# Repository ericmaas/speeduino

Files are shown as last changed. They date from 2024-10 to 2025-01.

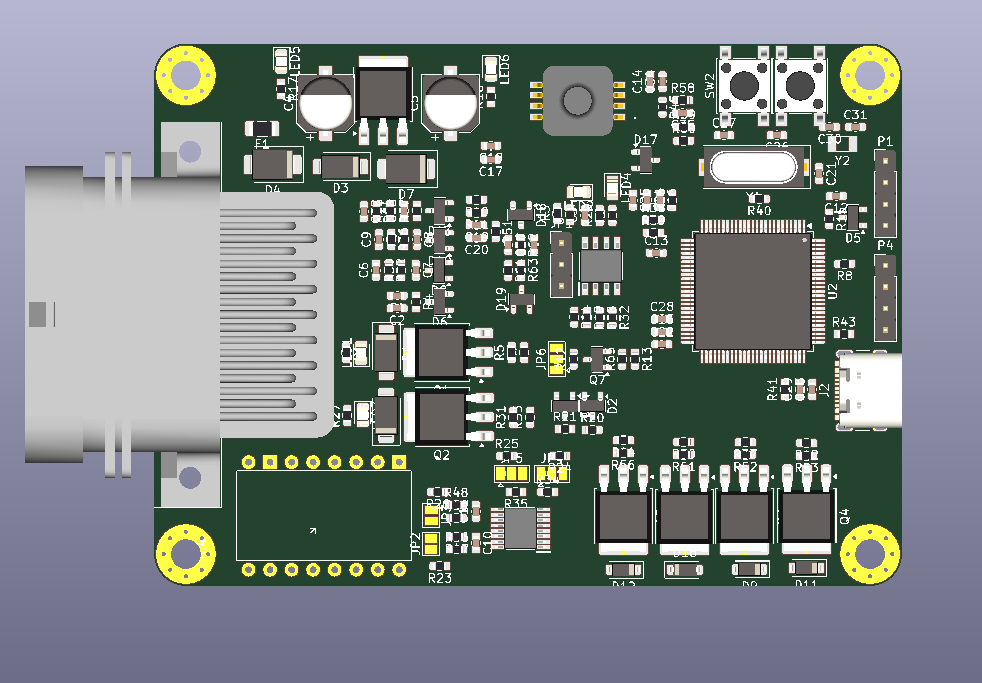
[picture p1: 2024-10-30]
NO2C-SMD/vDD1 - SMD/RENDER/Ideation/top-4layer-render.jpg

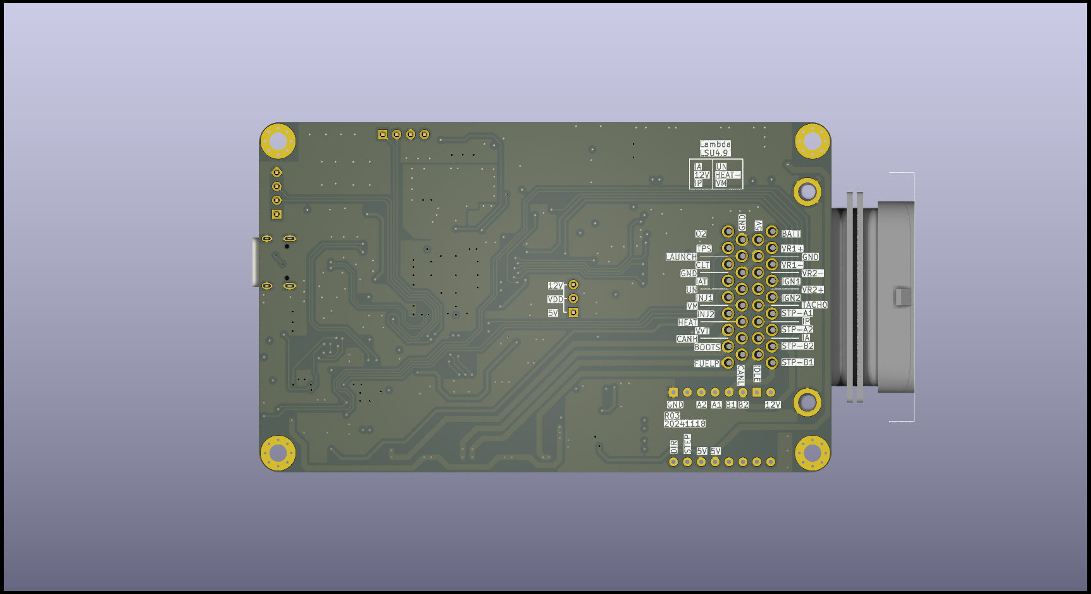
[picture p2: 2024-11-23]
NO2C-SMD/vDD3-SMDWBBT/RENDER/NO2C-2.png

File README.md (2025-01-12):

## NO2C vDD

All Credit to the Speeduino Team
https://github.com/speeduino/speeduino

And 

https://github.com/turboedge/SpeedyBoards/

Originally forked from:
https://github.com/turboedge/SpeedyBoards/tree/master

Wideband ideation from:
https://github.com/oelprinz-org

Please review my workprior to printing, and test your work. 

I am not an engineer, mechanic, or automotive specialist, please use at your own risk.

Please review vehicle laws and regulations prior to use. 

Connector used is a TE # 3-6437285-0

Future Feature Wish List:

- SD Card for data logging
- Dedicated prototyping pins (would be great for oil pressure)

The No Overhang Two Channel was designed to incorporate as many features as possible into a SMD board that moves to a new smaller format size. Microcontroller onboard. It is a 2+2 channel board that incorporates the features below.
- Two injector channels
- Two ignitor channels
- Outputs for VVT PWM idle, boost, fuel pump, and tachometer
- Two trigger inputs
- Launch input
- Analog inputs for CLT, IAT, TPS, and O2
- MAP sensor onboard
- Socket for stepper idle control module
- Additional pins for i2c and canbus
- LSU 4.9 Wideband integration
- Bluetooth 4.0 (HM-10)

Latest version: DD3

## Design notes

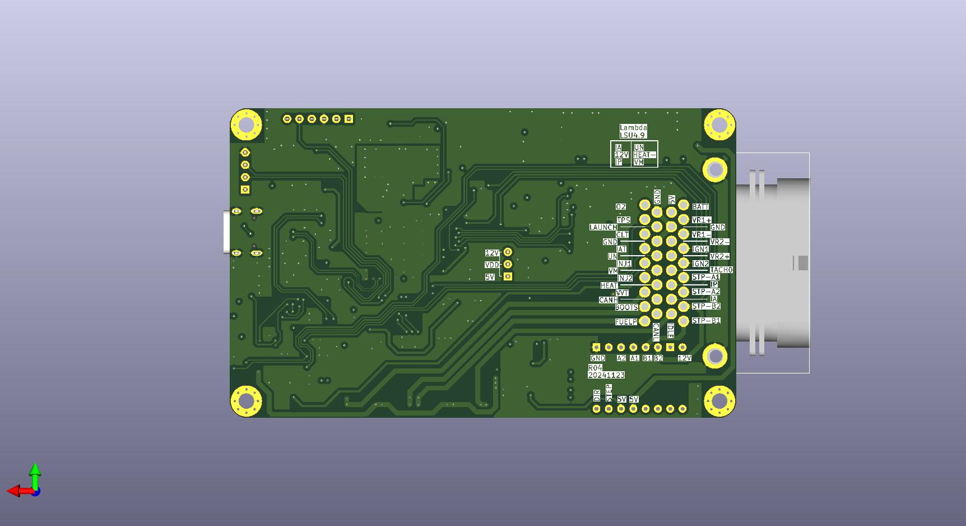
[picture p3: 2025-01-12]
NO2C-SMD/vDD3-SMDWBBT/RENDER/NO2C.jpg

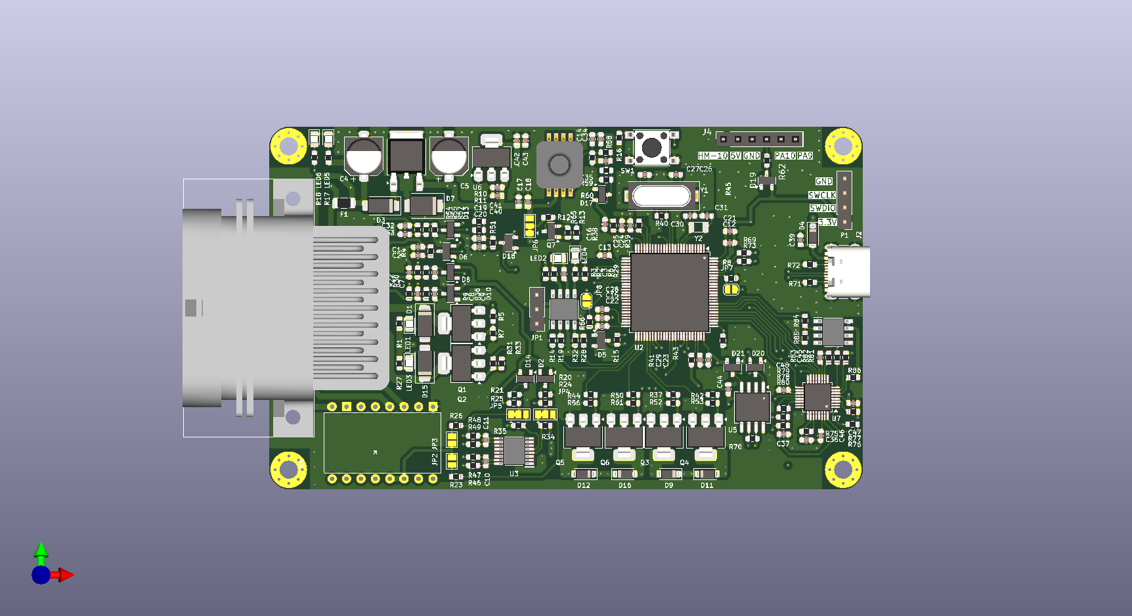
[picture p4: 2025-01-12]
NO2C-SMD/vDD3-SMDWBBT/RENDER/NO2C.png

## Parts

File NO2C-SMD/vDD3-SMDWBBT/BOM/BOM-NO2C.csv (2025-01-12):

Comment | Designator | Footprint | LCSC | Quantity
22pF | C26,C27 | C_0603_1608Metric | C105620 | 2
47pF | C14 | C_0603_1608Metric | C105622 | 1
12pF | C30,C31 | C_0603_1608Metric | C107034 | 2
220nF | C2,C20,C33,C35,C7,C9 | C_0603_1608Metric | C107083 | 6
10uF | C39,C41,C42 | C_0603_1608Metric | C109457 | 3
8Mhz | Y1 | Crystal_SMD_HC49-SD | C12674 | 1
2K7 | R17 | R_0603_1608Metric | C13167 | 1
60V 1A | D3 | D_SMA | C134421 | 1
100nF | C1,C13,C15,C16,C17,C18,C19,C21,C22,C23,C25,C28,C29,C3,C32,C34,C36,C40,C43,C44,C45,C46,C47,C48,C6,C8 | C_0603_1608Metric | C14663 | 26
MAX9926UAEE+ | U3 | SOP64P602X175-16N | C1523548 | 1
1A 60V | F1 | Fuse_1206_3216Metric | C163133 | 1
1nF | C10,C11,C12,C24 | C_0603_1608Metric | C1636 | 4
USB_C_Receptacle_USB2.0_16P | J2 | USB_C_Receptacle_GCT_USB4105-xx-A_16P_TopMnt_Horizontal | C165948 | 1
CJ125_32 | U7 | LQFP-32_5x5mm_P0.5mm | C18198890 | 1
0R | R38,R39 | R_0603_1608Metric | C21189 | 2
1K | R12,R14,R15,R23,R26,R28,R34,R35,R69,R73 | R_0603_1608Metric | C21190 | 10
100R | R13,R31,R37,R42,R44,R5,R50 | R_0603_1608Metric | C22775 | 7
120R | R70 | R_0603_1608Metric | C22787 | 1
2K49 | R22,R9 | R_0603_1608Metric | C22908 | 2
1M | R40 | R_0603_1608Metric | C22935 | 1
2K | R1,R2,R27,R6 | R_0603_1608Metric | C22975 | 4
61.9R | R76 | R_0603_1608Metric | C23092 | 1
4K7 | R55,R59 | R_0603_1608Metric | C23162 | 2
470R | R18,R24,R25,R30,R36,R4,R51,R54,R58,R62 | R_0603_1608Metric | C23179 | 10
47R | R29,R3 | R_0603_1608Metric | C23182 | 2
5.1K | R71,R72 | R_0603_1608Metric | C23186 | 2
51K | R11,R45 | R_0603_1608Metric | C23196 | 2
9K1 | R57,R60 | R_0603_1608Metric | C23260 | 2
100K | R19,R32,R75,R80,R85 | R_0603_1608Metric | C25803 | 5
10K | R16,R20,R21,R33,R41,R43,R46,R47,R48,R49,R52,R53,R56,R61,R65,R66,R7,R77,R8,R81,R82,R83 | R_0603_1608Metric | C25804 | 22
6.8K | R86 | R_0603_1608Metric | C26004 | 1
BSP78HUMA1 | Q1,Q2,Q3,Q4,Q5,Q6 | SOT-223-3_TabPin2 | C2653794 | 6
MPXH6400AC6T1 | IC2 | MPXH6400AC6T1 | C2828031 | 1
STM32F407VETx | U2 | LQFP-100_14x14mm_P0.5mm | C28730 | 1
1N4007-A7 | D11,D12,D16,D4,D9 | D_SOD-123 | C2902912 | 5
2.2nF | C37 | C_0603_1608Metric | C309517 | 1
32.768Khz | Y2 | Crystal_SMD_3215-2Pin_3.2x1.5mm | C32346 | 1
47u 50v | C4,C5 | CP_Elec_6.3x7.7 | C3349 | 2
AO3400A | Q7 | SOT-23 | C344010 | 1
470K | R78 | R_0603_1608Metric | C365173 | 1
HM-10 | J4 | PinSocket_1x06_P2.54mm_Vertical | C40877 | 1
33K | R10 | R_0603_1608Metric | C4216 | 1
TC4424AVOA | IC1 | SOIC127P600X175-8N | C44150 | 1
BAT54S | D10,D13,D14,D17,D18,D19,D2,D20,D21,D5,D6,D8 | SOT-23 | C47546 | 12
ING-VLT | JP1 | PinHeader_1x03_P2.54mm_Vertical | C49257 | 1
VNS3NV04DPTR-E | IC3 | SOIC127P600X175-8N | C503069 | 1
Conn_01x04 | P1 | PinHeader_1x04_P2.54mm_Vertical | C5116483 | 1
SW_Push | SW1 | SW_Push_1P1T_NO_6x6mm_H9.5mm | C5127964 | 1
AMS1117-3.3 | U6 | SOT-223-3_TabPin2 | C6186 | 1
TJA1050 | U5 | SO-8_5.3x6.2mm_P1.27mm | C6952 | 1
1N4004 | D1,D15 | D_SMA | C727080 | 2
L7805CDT(UMW) | U1 | TO-252-2 | C7394043 | 1
1SMB5919BT3G | D7 | D_SMB | C7422622 | 1
RED | LED1,LED2,LED3,LED4,LED5,LED6 | LED_0805_2012Metric | C84256 | 6
4.7K | R79,R84 | R_0603_1608Metric | C99782 | 2
3-6437285-0 | J1 | 364372850 |  | 1

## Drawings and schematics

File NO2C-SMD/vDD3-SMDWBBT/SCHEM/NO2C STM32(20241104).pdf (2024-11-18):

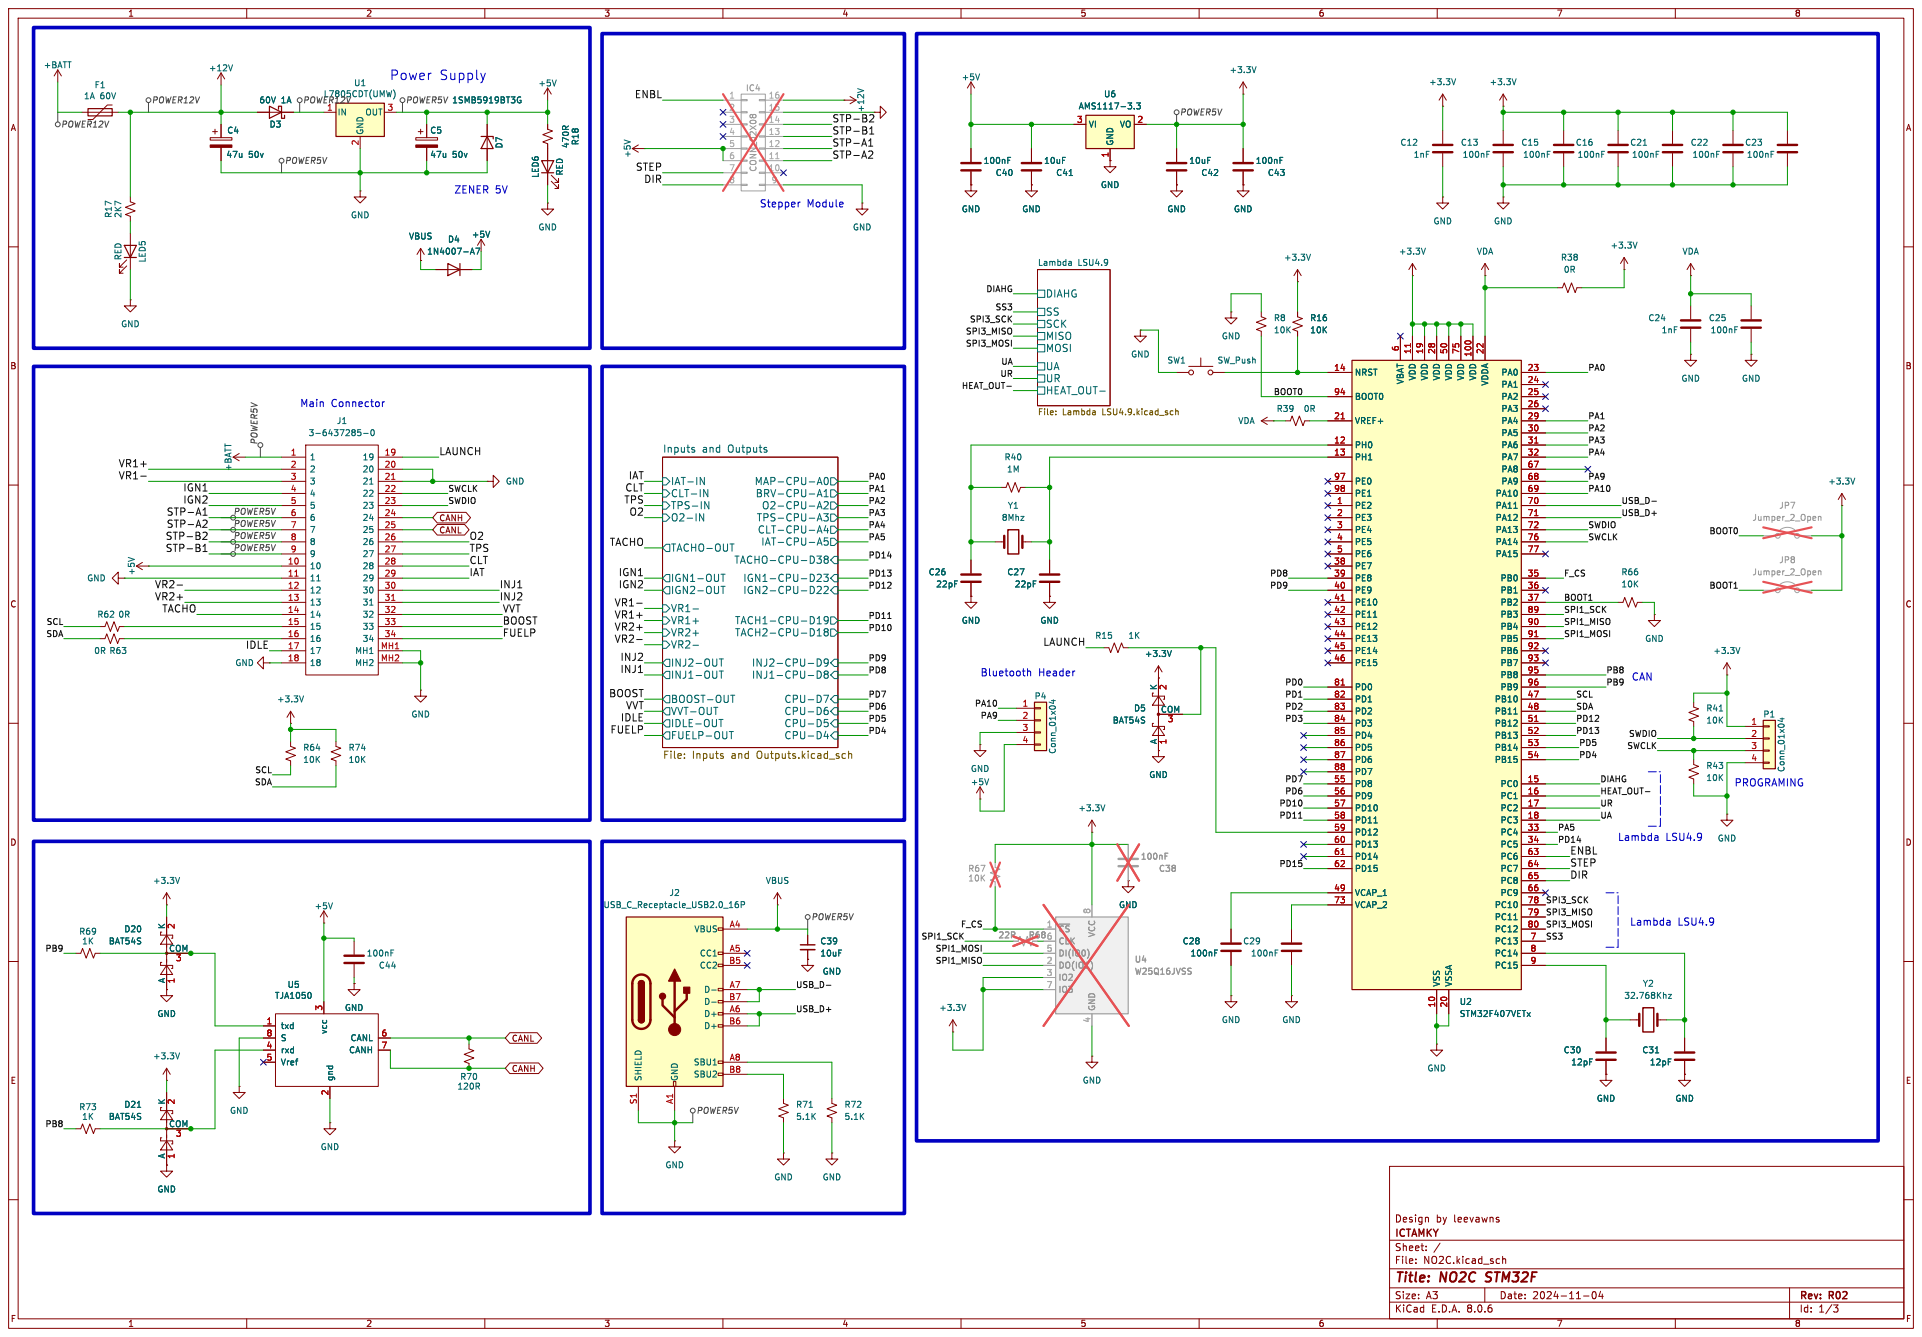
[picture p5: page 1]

Power Supply Main Connector

HEAT_OUT- Lambda LSU4.9 File: Lambda LSU4.9.kicad_sch GND GND

ICTAMKY Design by leevawns

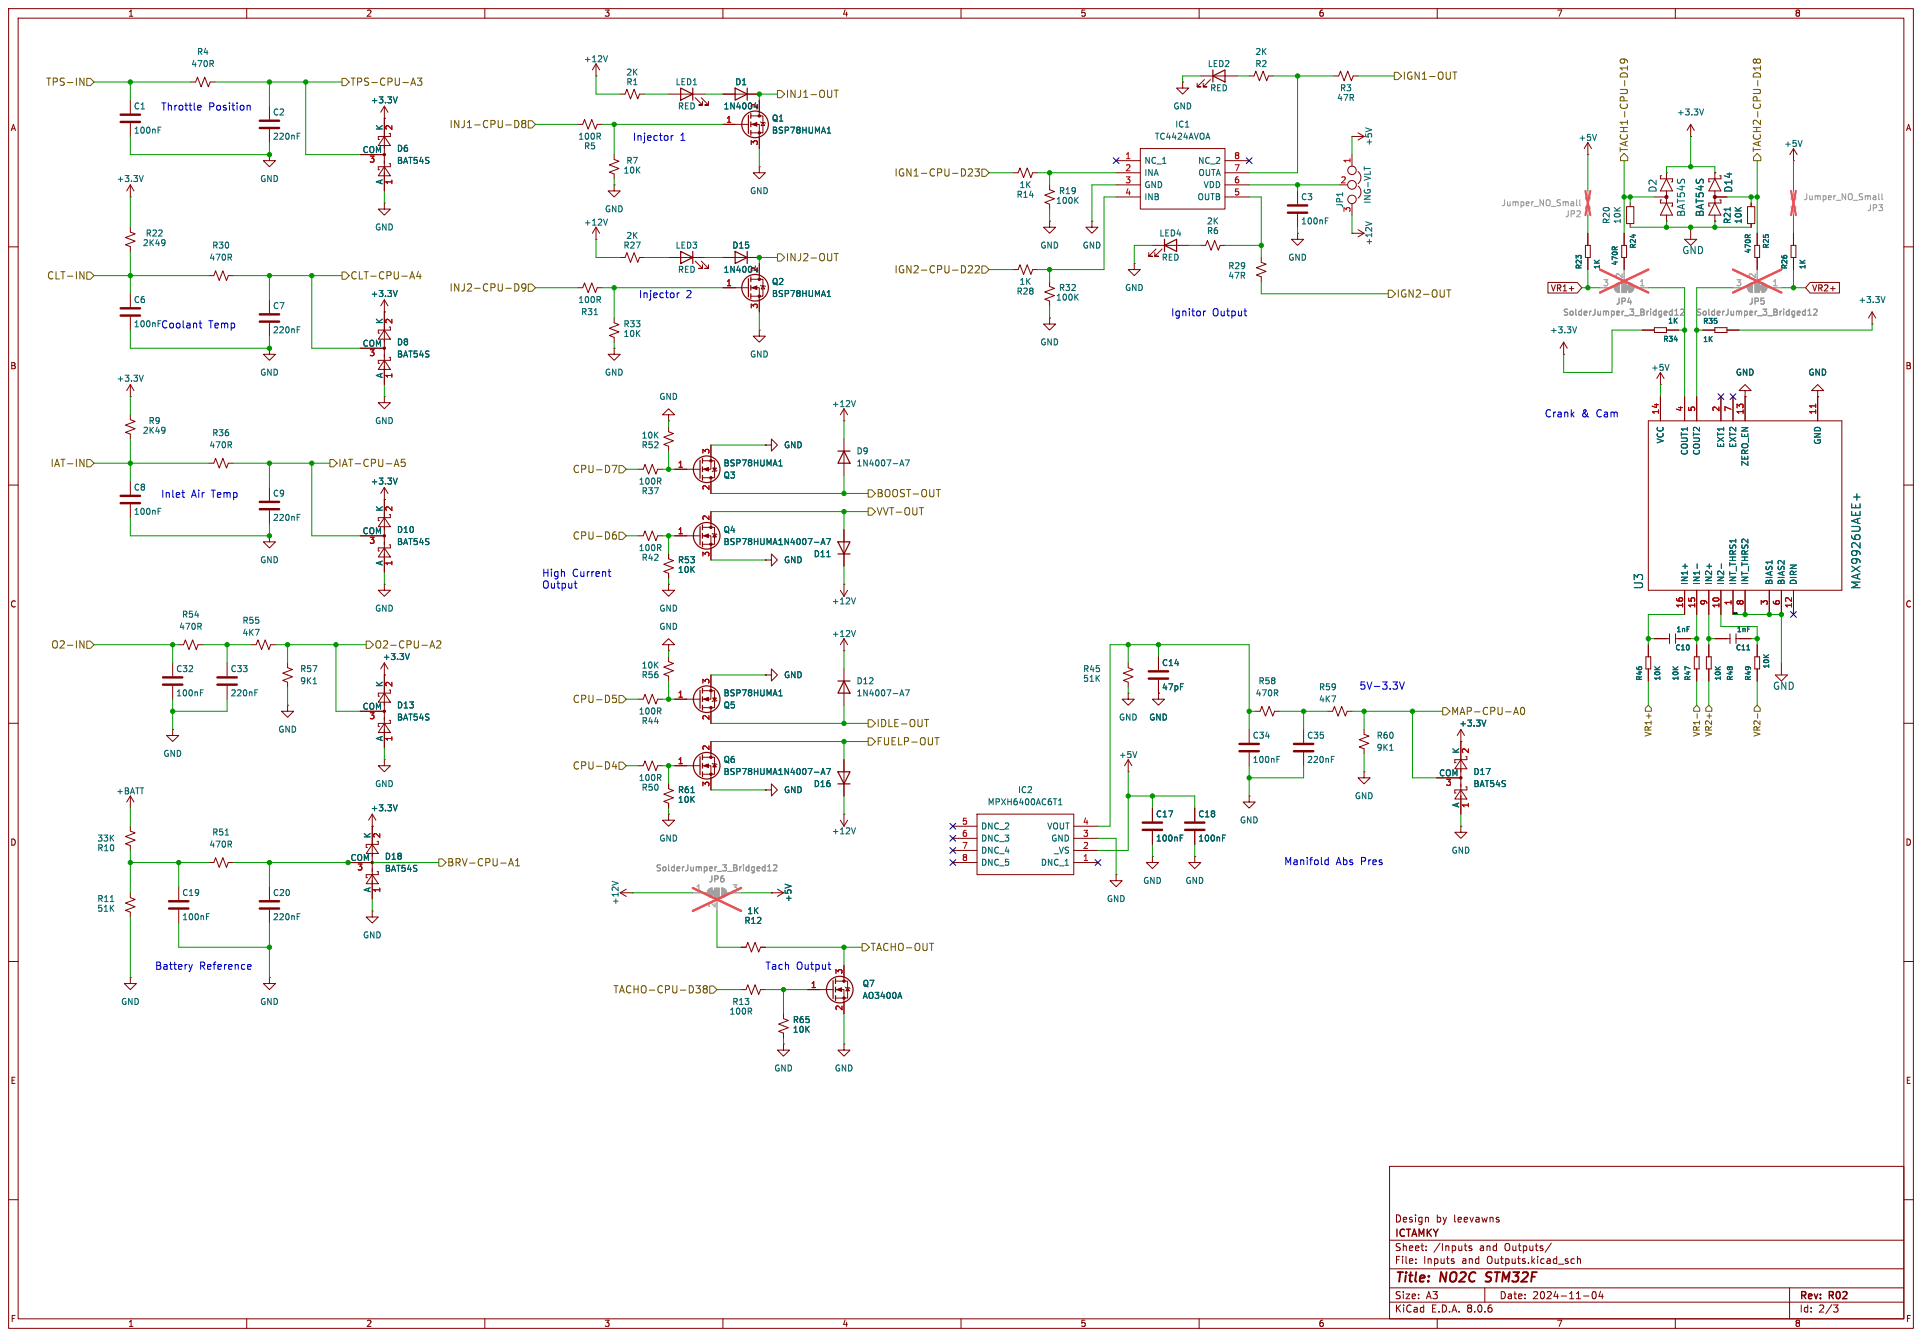
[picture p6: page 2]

ICTAMKY Design by leevawns

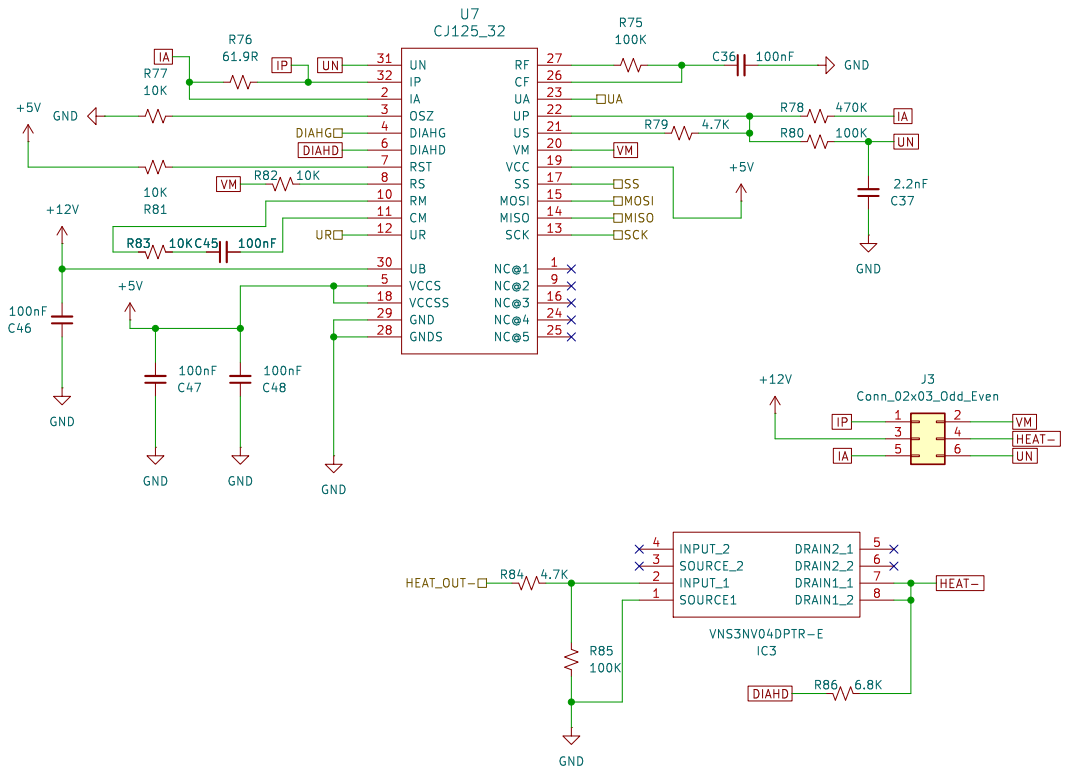
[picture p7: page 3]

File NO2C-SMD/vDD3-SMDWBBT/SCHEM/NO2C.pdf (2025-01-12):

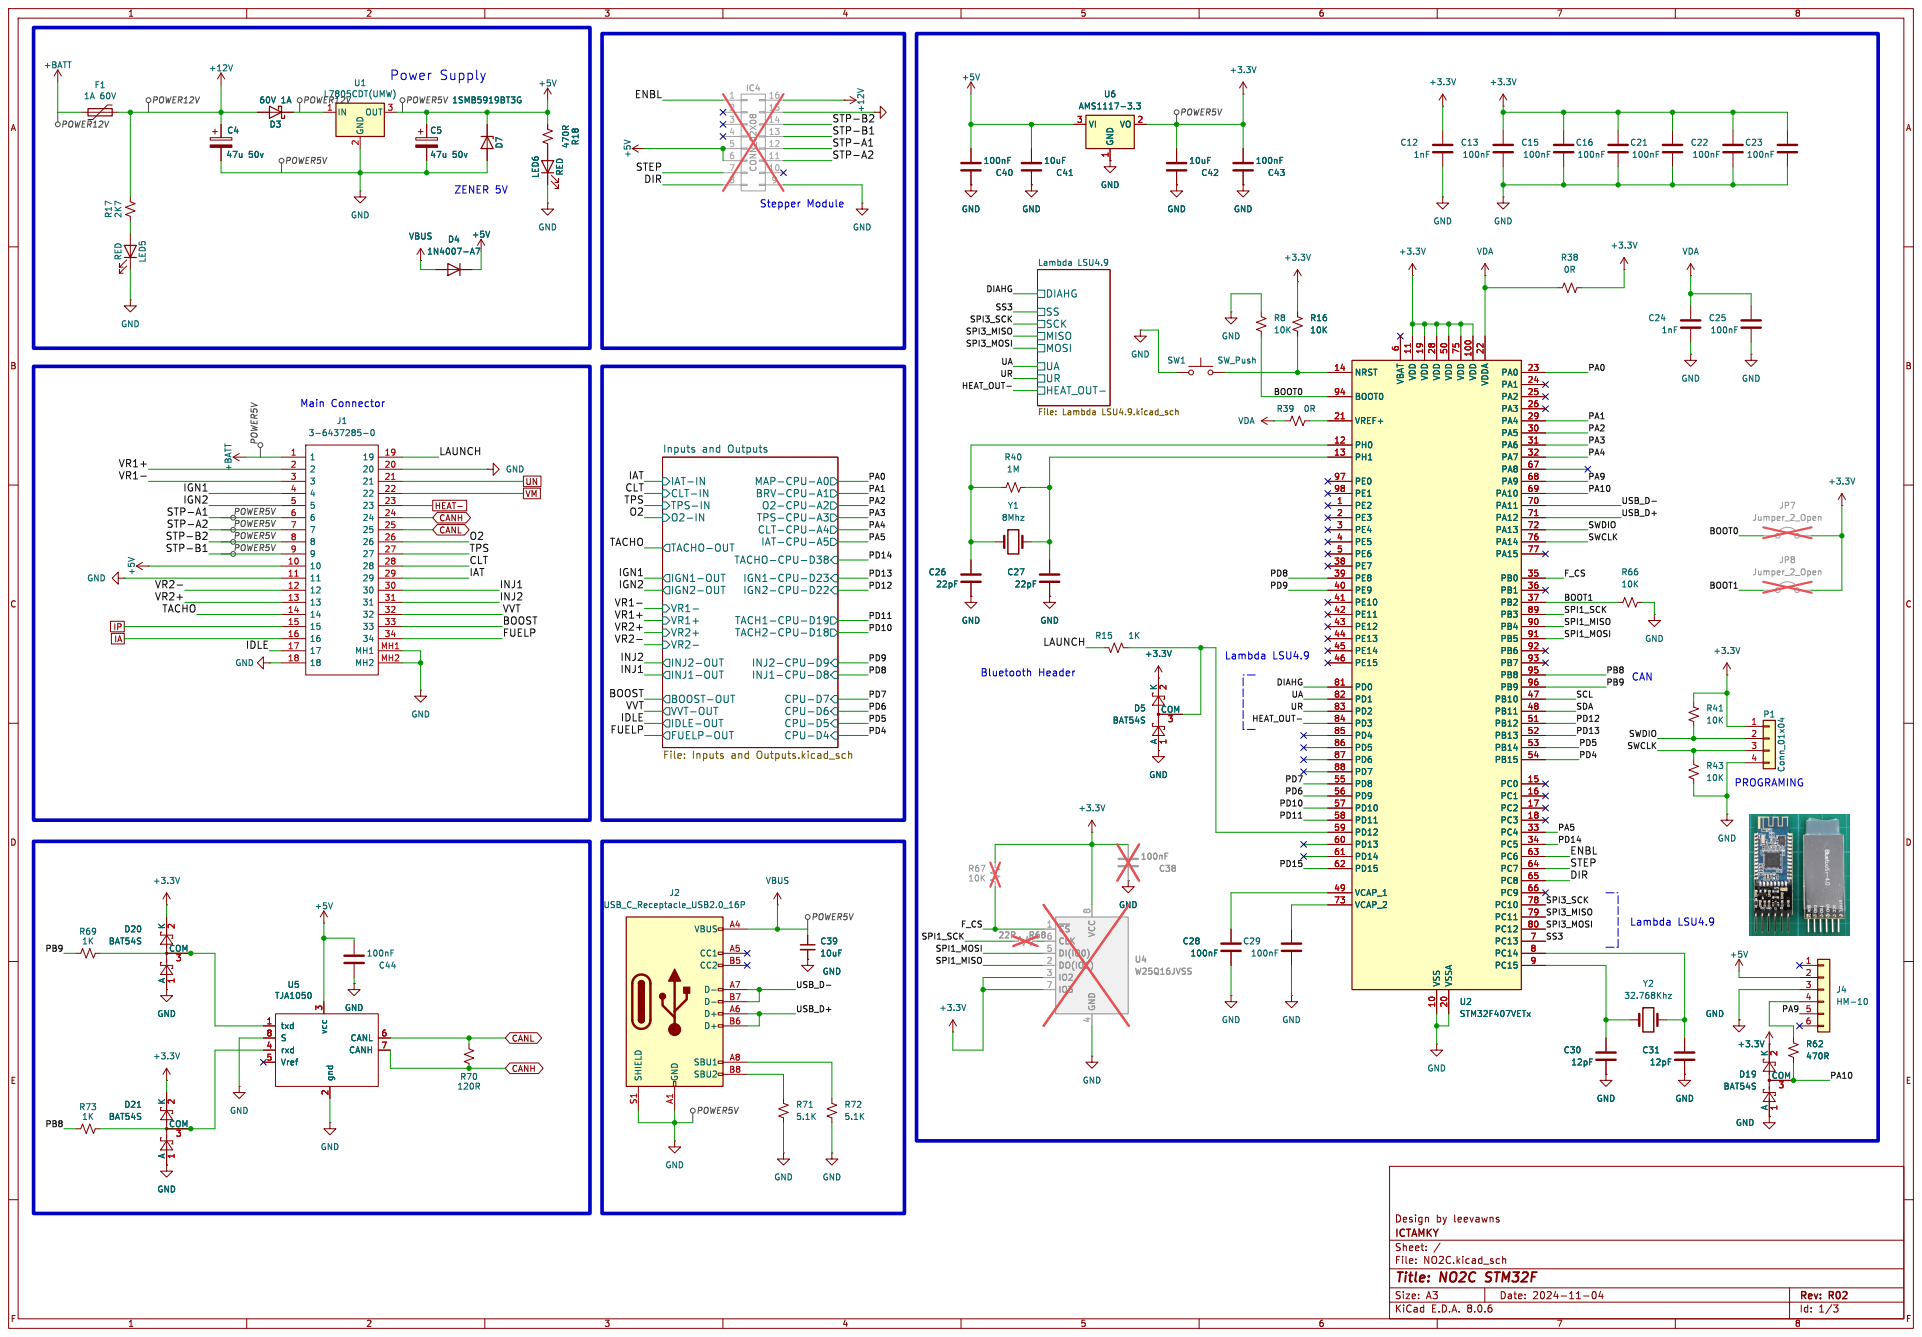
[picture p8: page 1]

ICTAMKY Design by leevawns

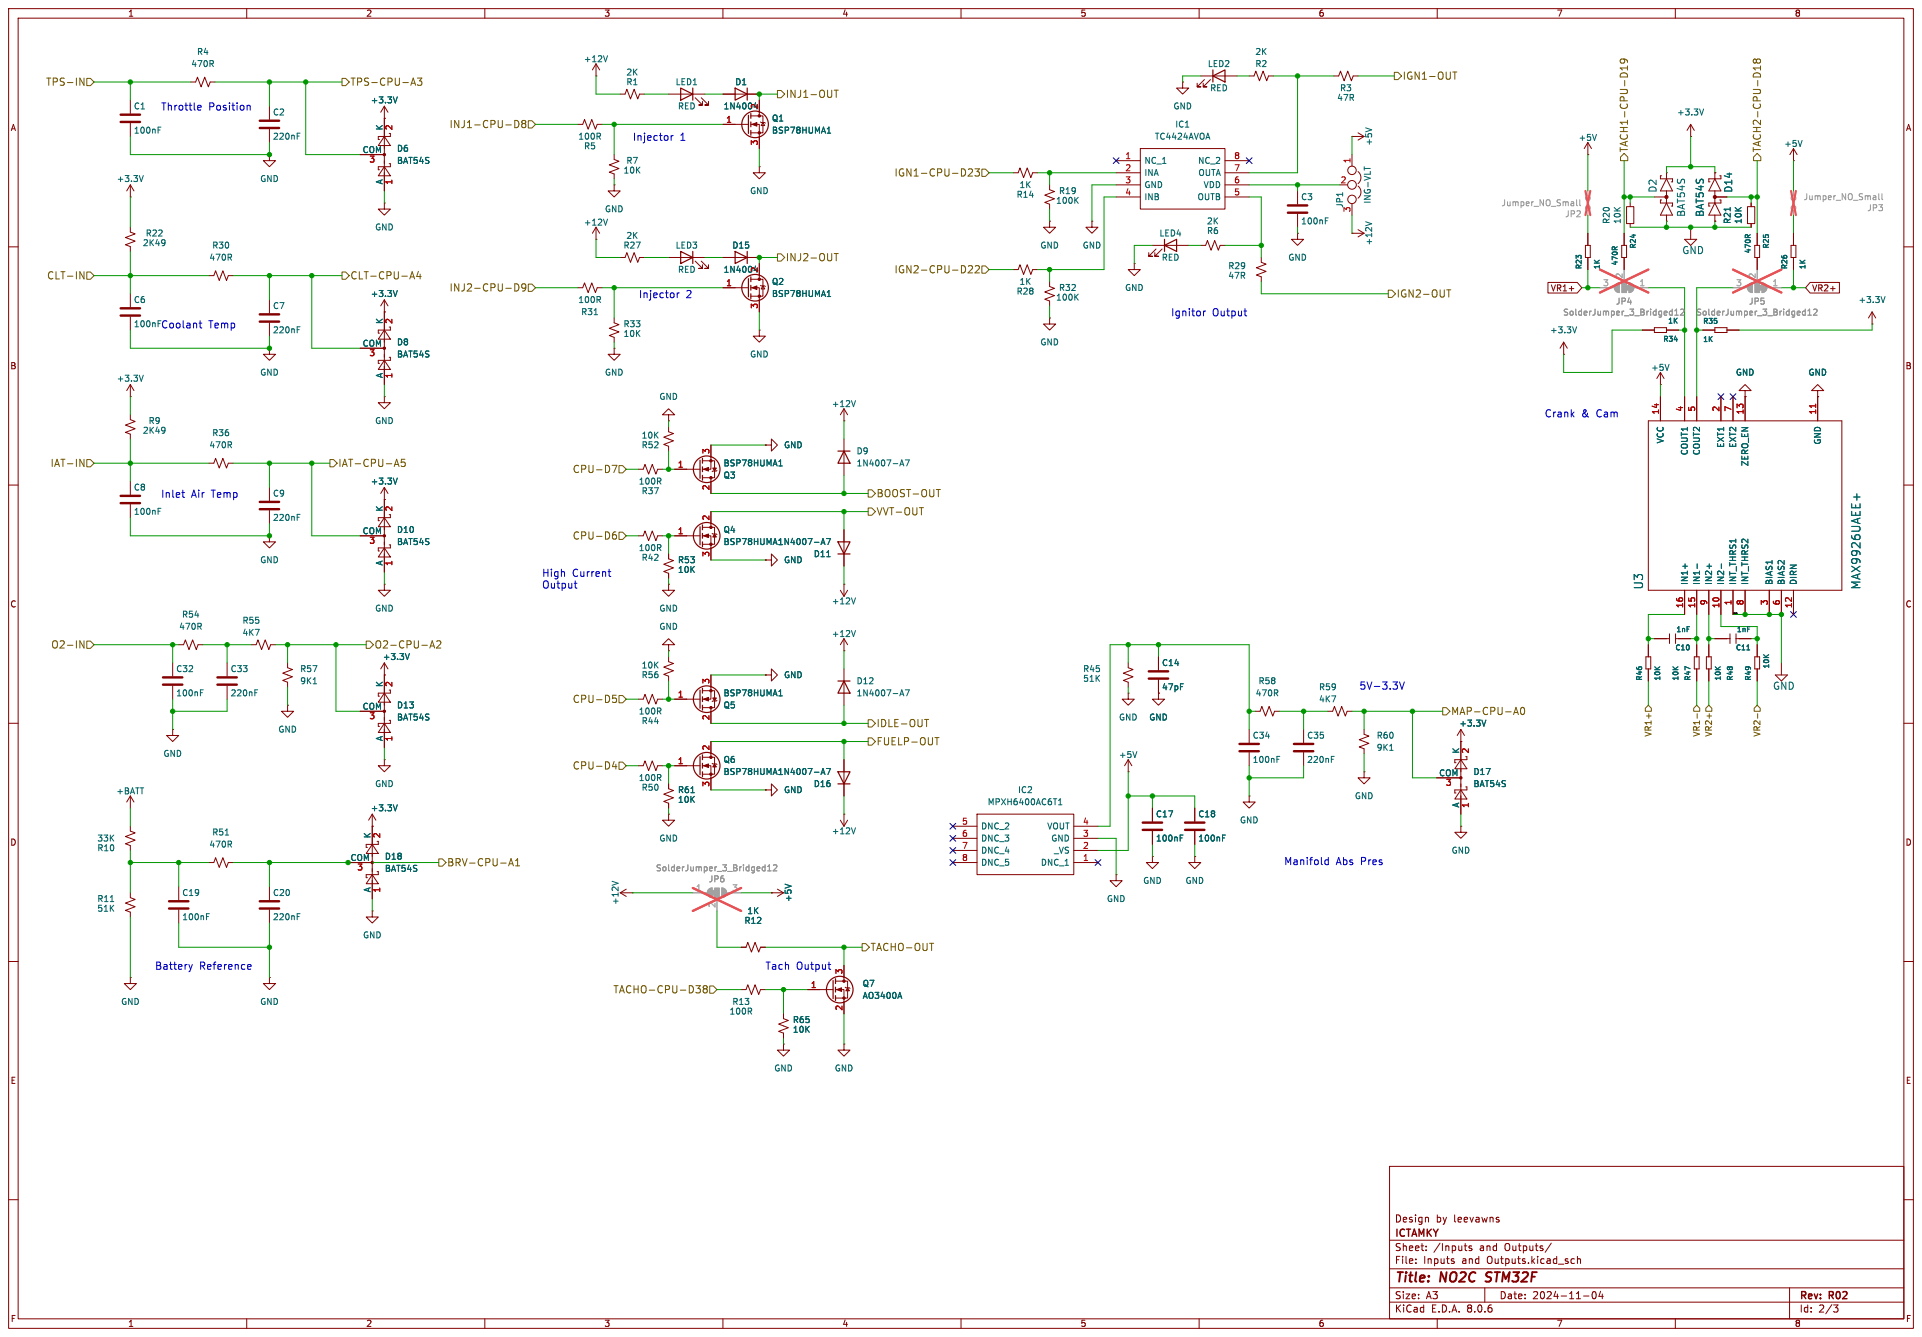
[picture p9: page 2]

ICTAMKY Design by leevawns

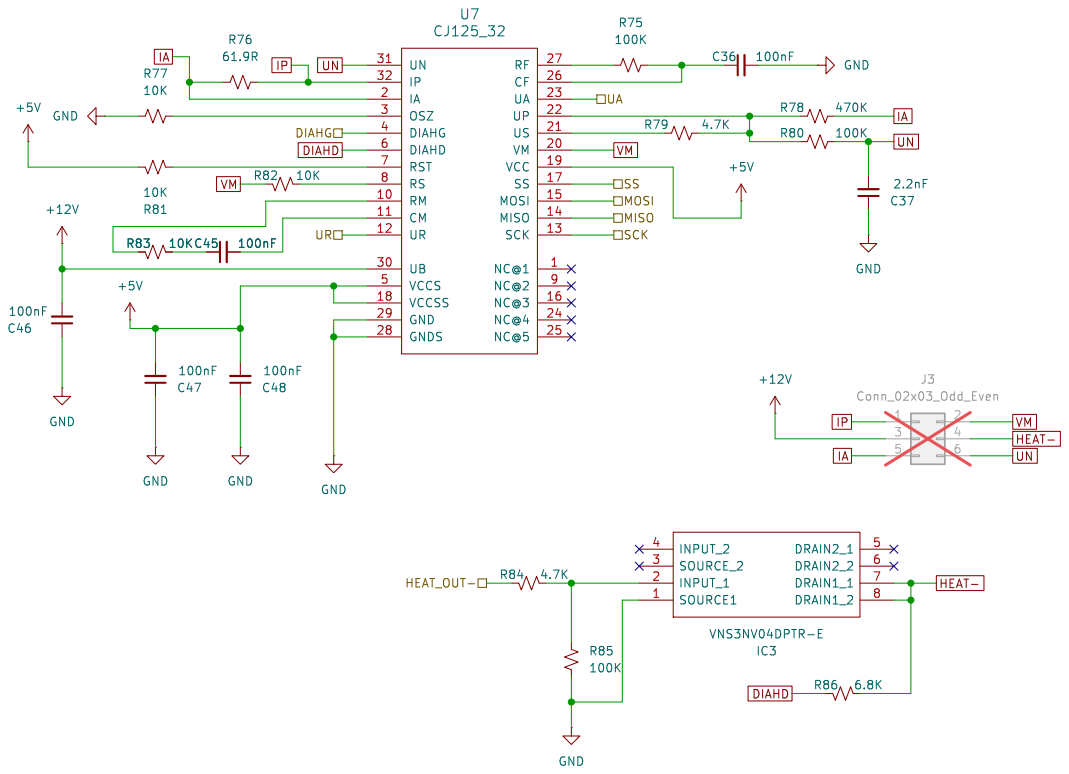
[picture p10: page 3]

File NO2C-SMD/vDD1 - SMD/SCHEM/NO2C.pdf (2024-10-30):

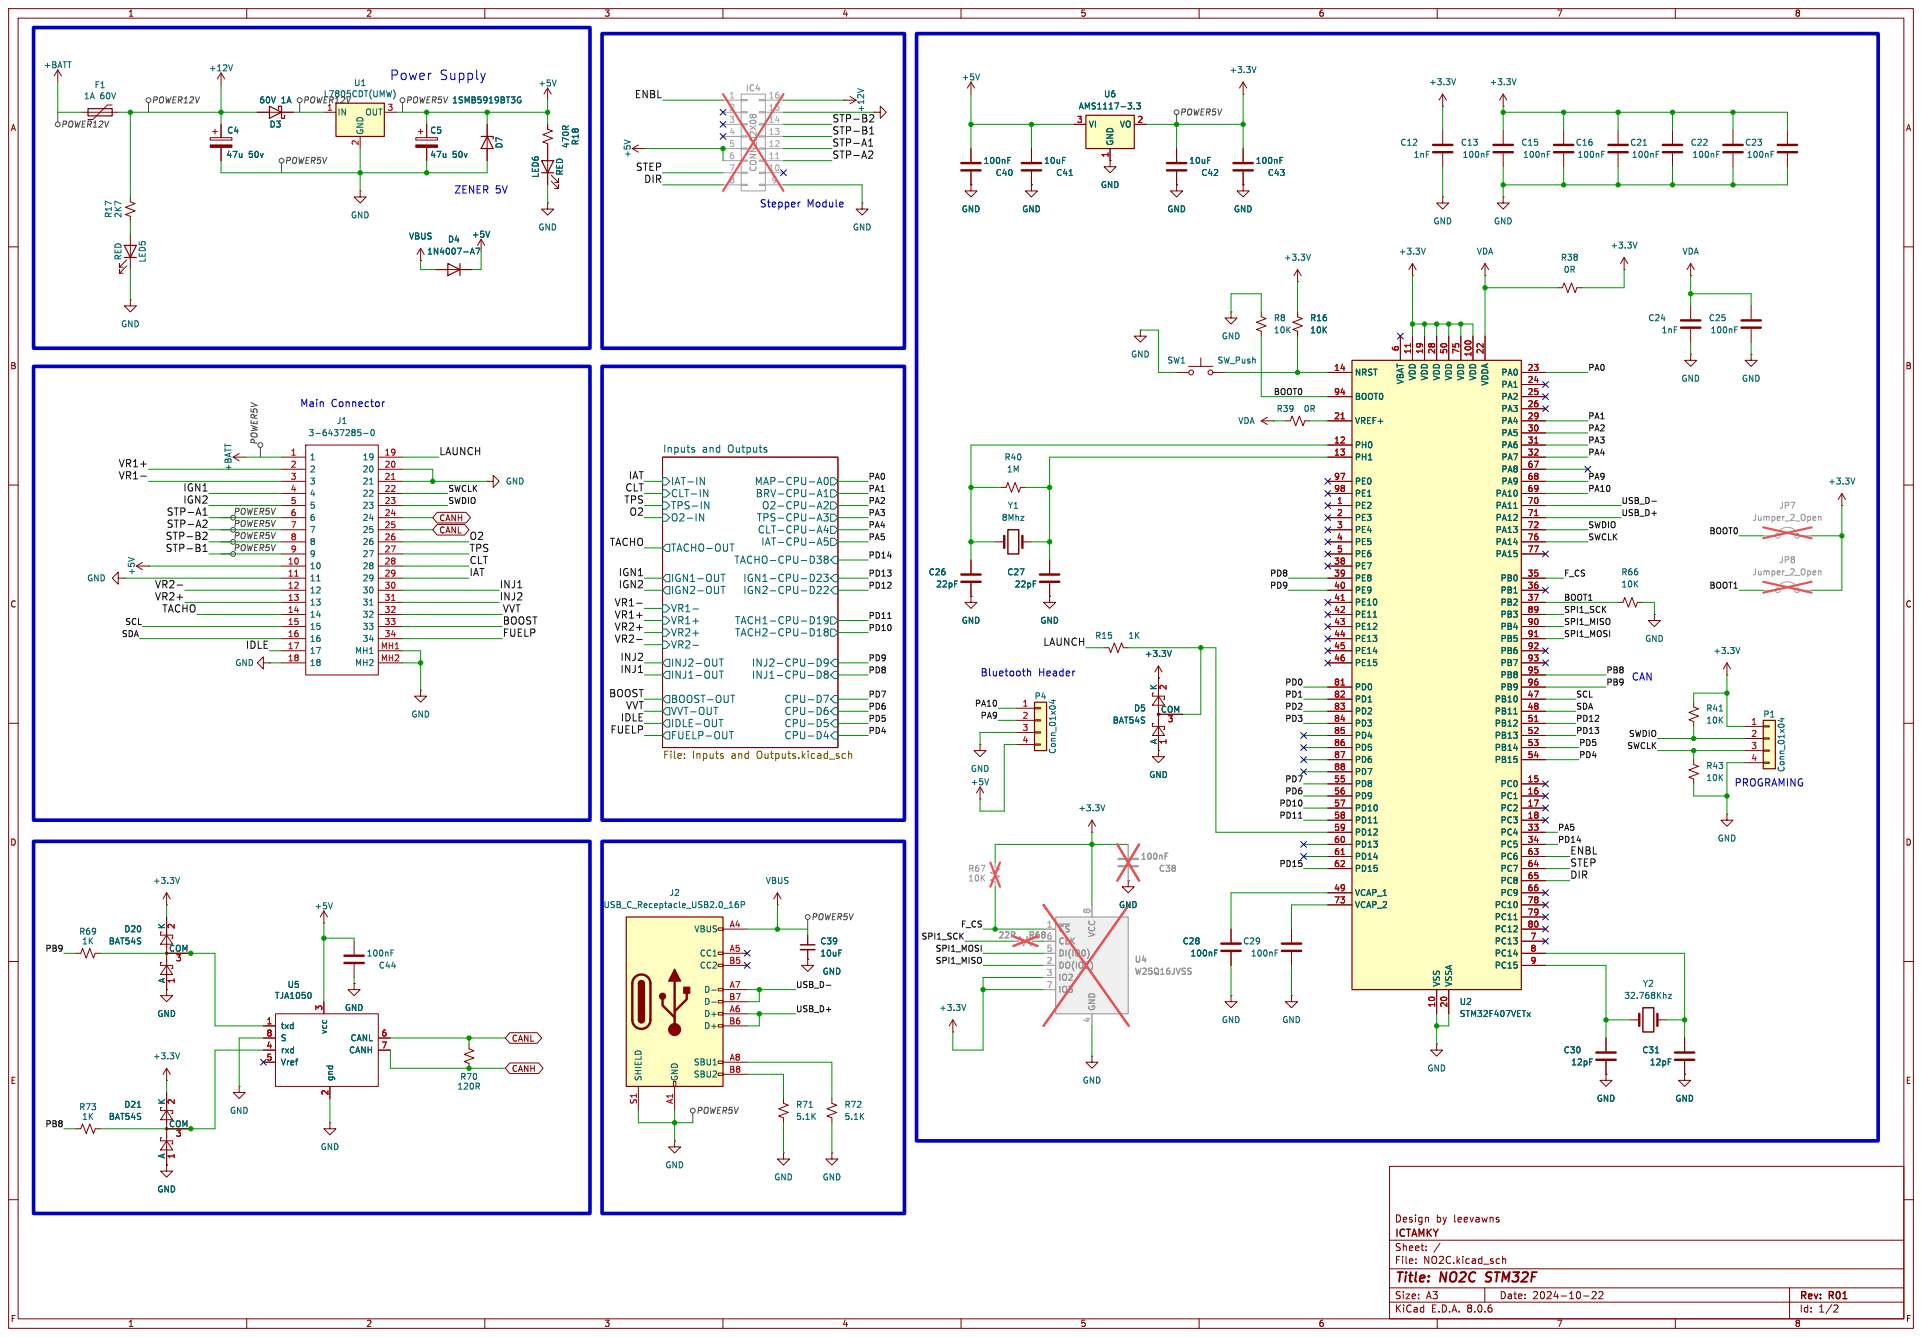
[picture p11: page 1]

ICTAMKY Design by leevawns

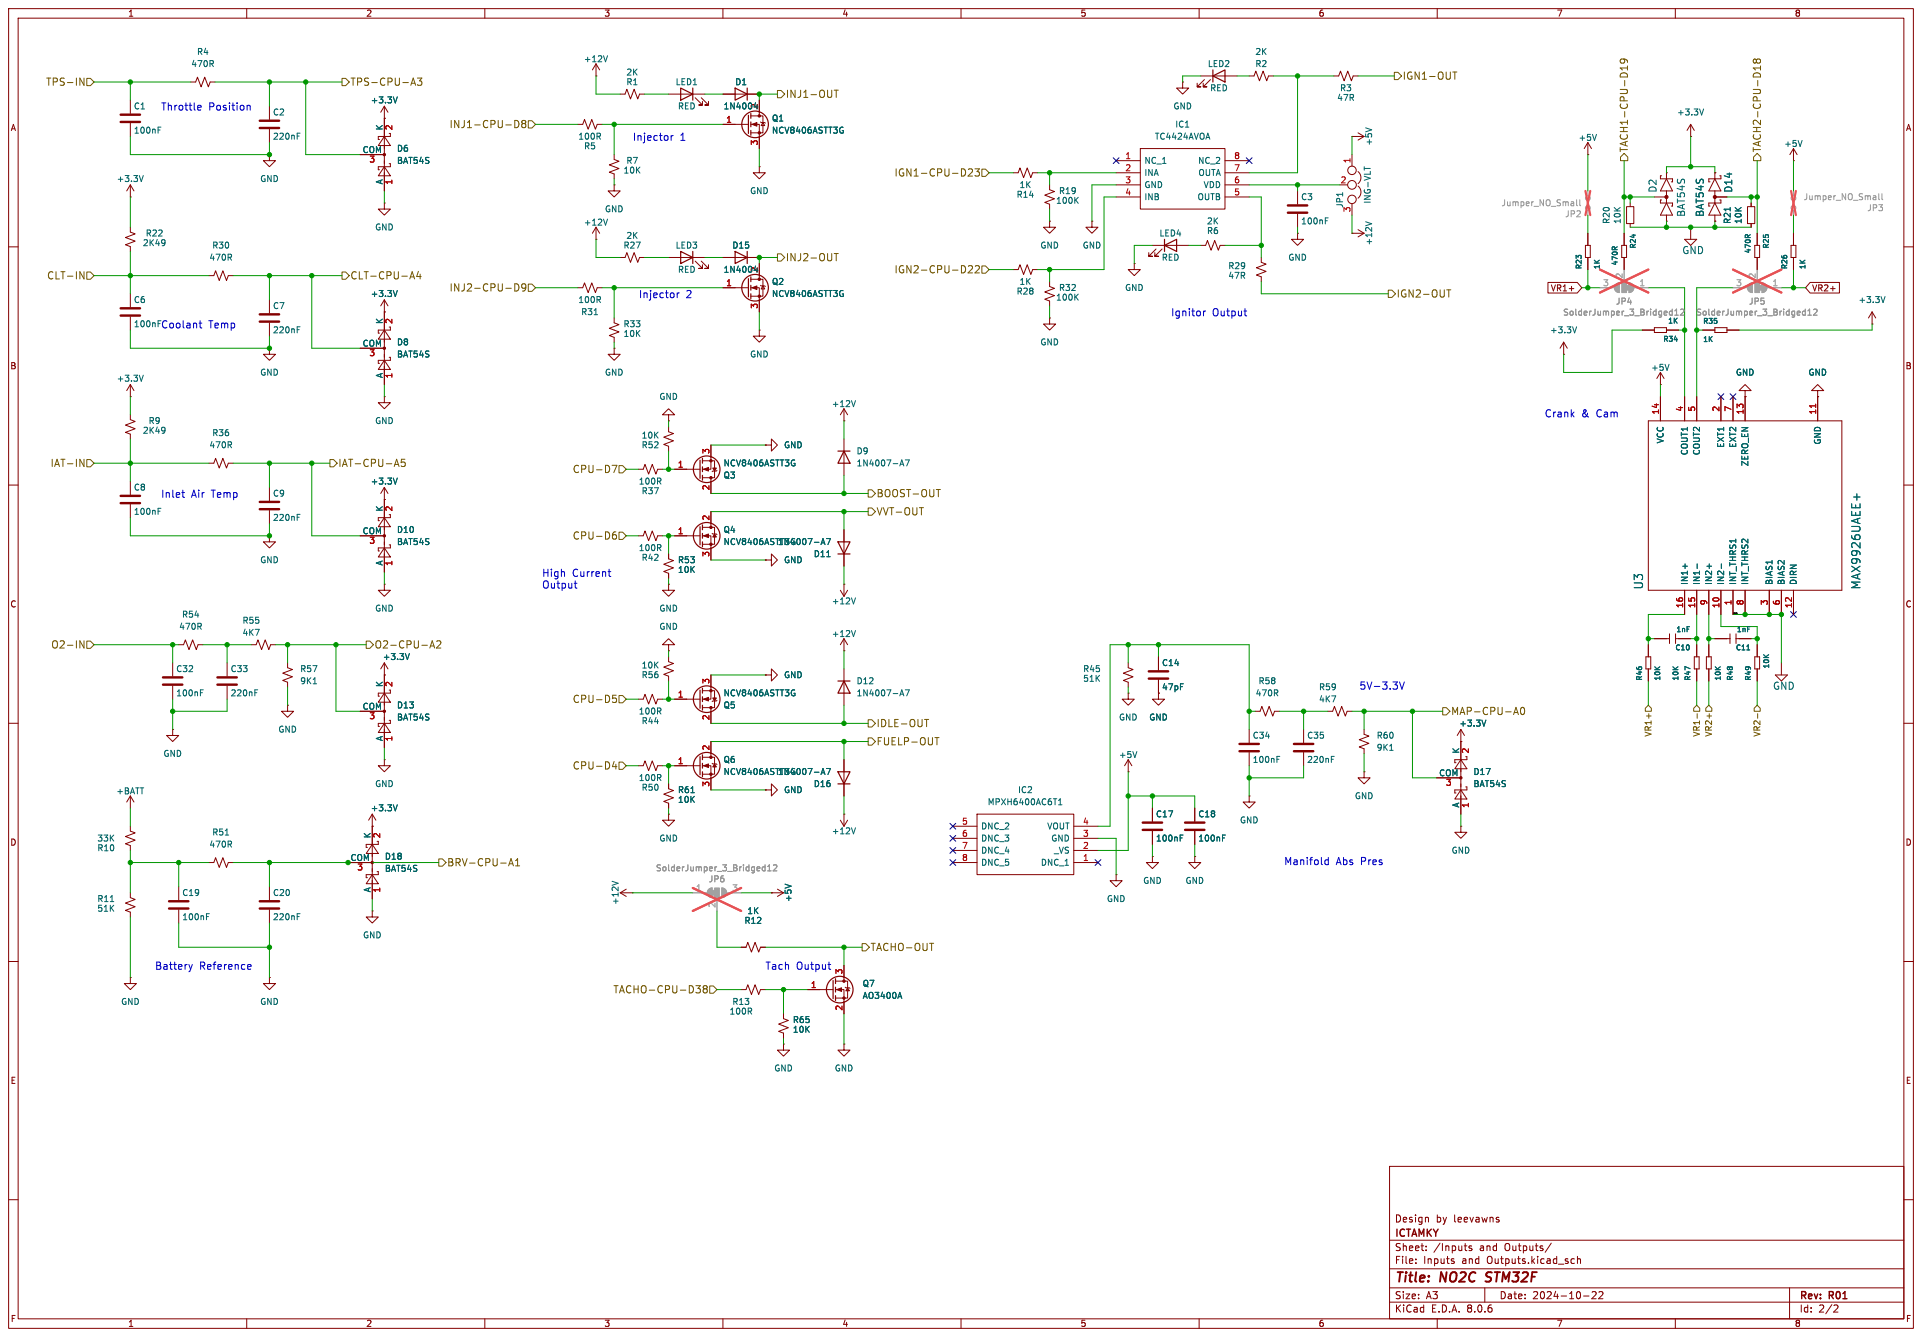
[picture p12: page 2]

ICTAMKY Design by leevawns

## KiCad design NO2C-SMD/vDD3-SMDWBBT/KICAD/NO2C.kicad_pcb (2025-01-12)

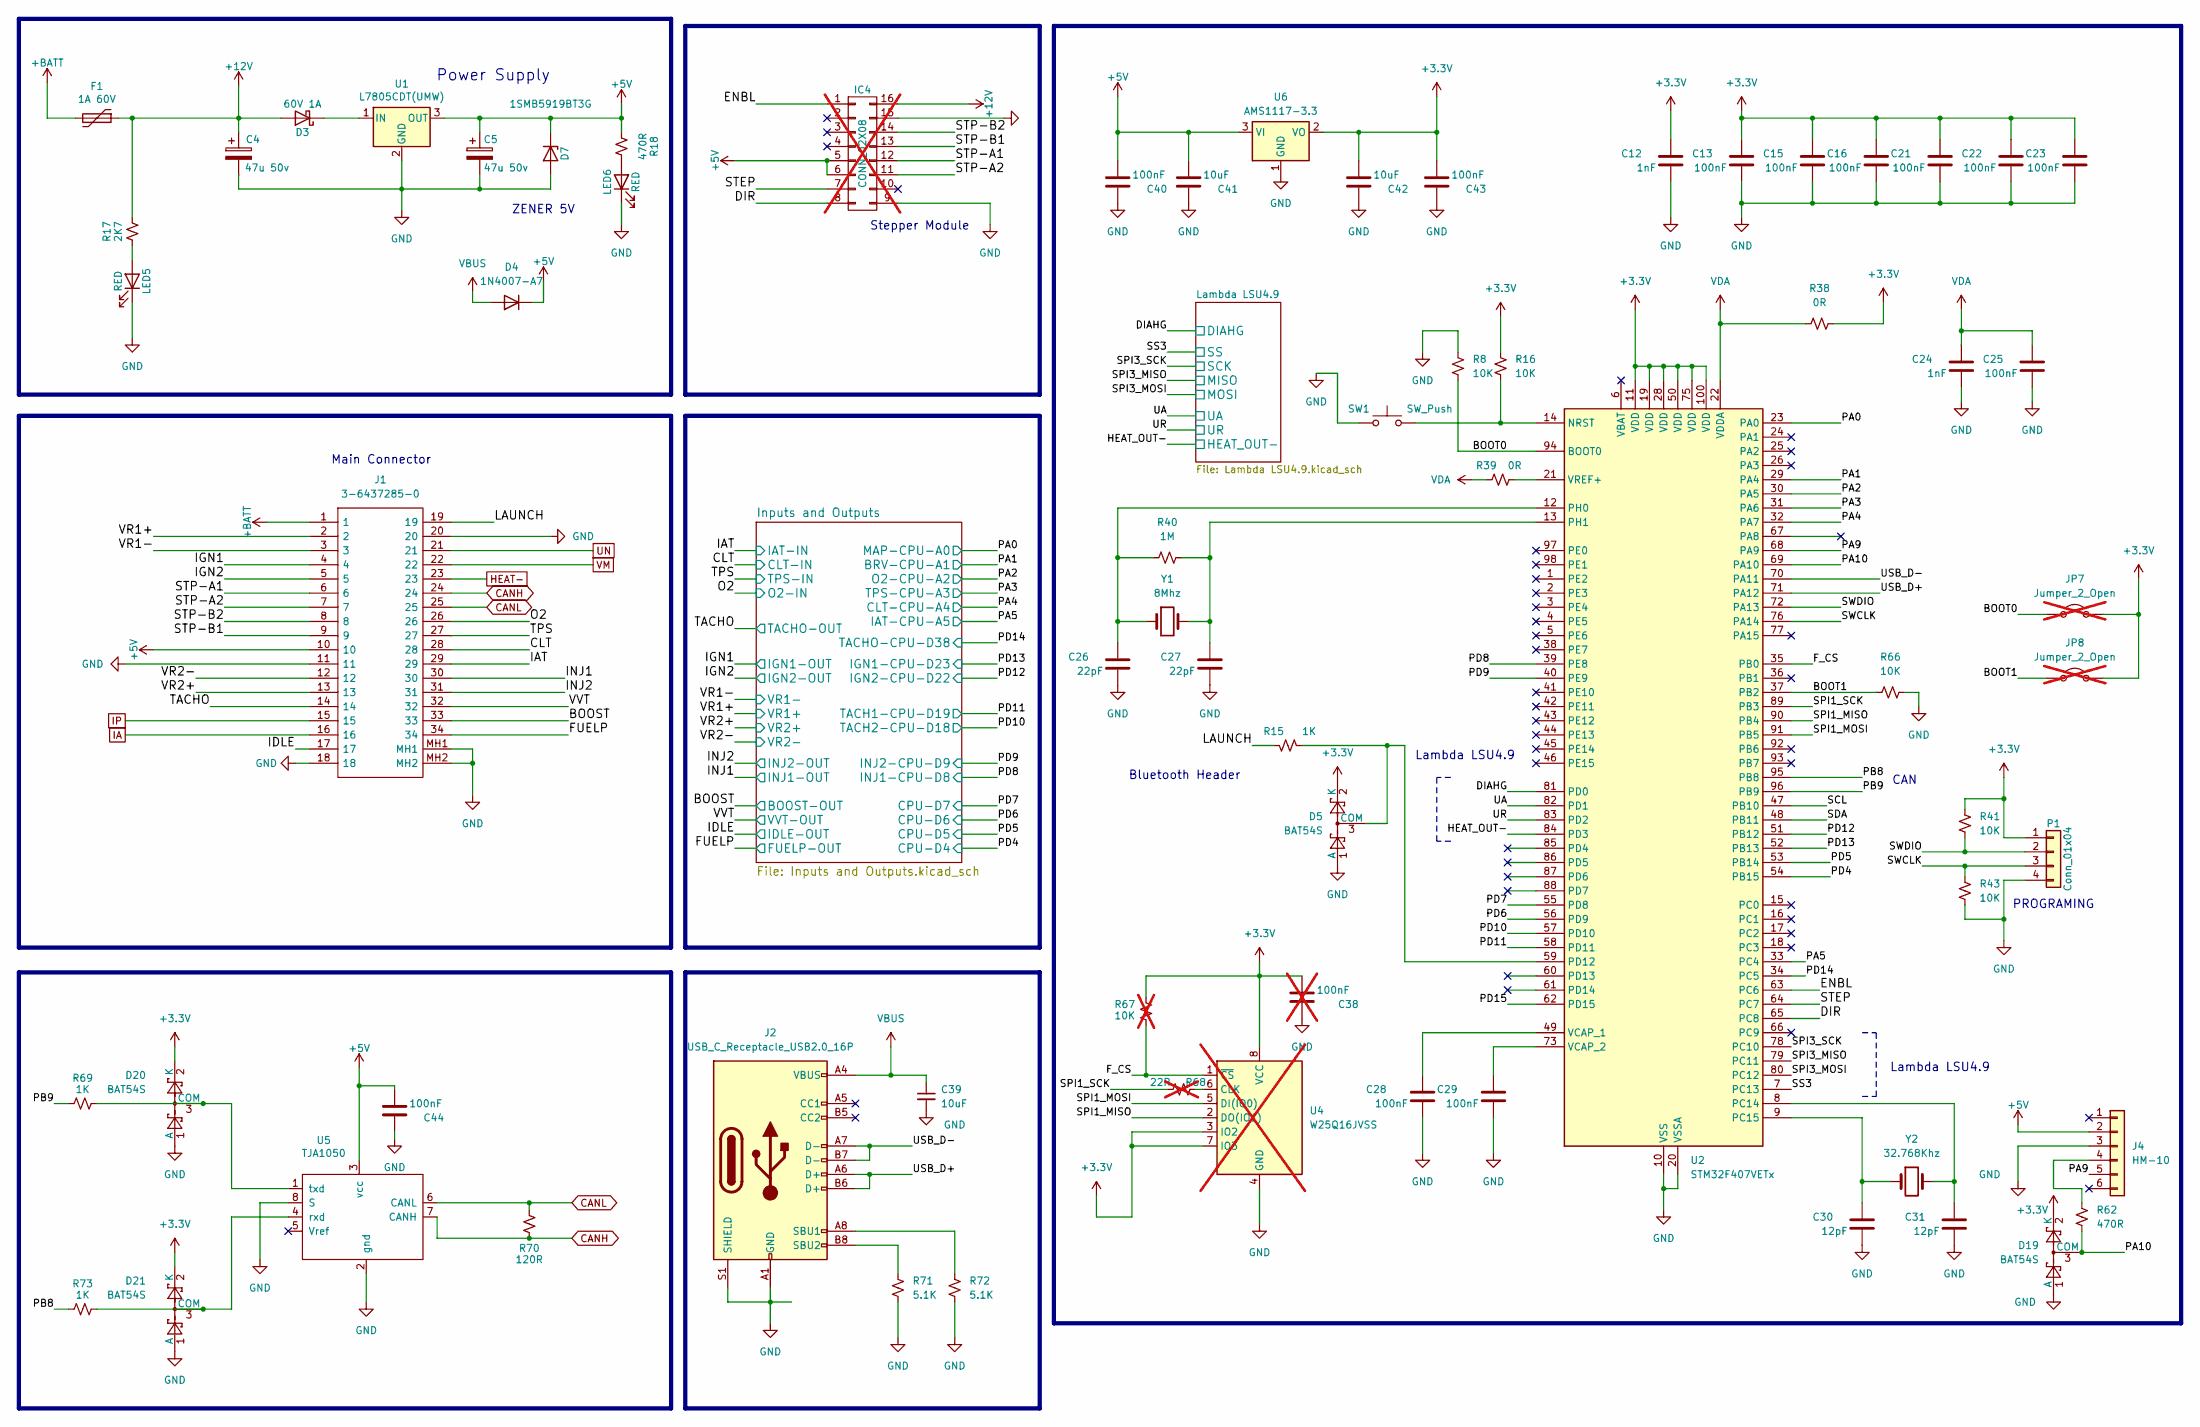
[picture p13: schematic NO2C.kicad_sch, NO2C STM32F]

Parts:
C4, C5: 47u 50v; CP_Elec_6.3x7.7; MPN RVT1H470M0607; LCSC Part C3349
C12, C24: 1nF; C_0603_1608Metric; MPN 0603CG102J500NT; LCSC Part C1636
C13, C15, C16, C21, C22, C23, C25, C28, C29, C40, C43, C44: 100nF; C_0603_1608Metric; MPN CC0603KRX7R9BB104; LCSC Part C14663
C26, C27: 22pF; C_0603_1608Metric; MPN CC0603JRNPO9BN220; LCSC Part C105620
C30, C31: 12pF; C_0603_1608Metric; MPN CC0603JRNPO9BN120; LCSC Part C107034
C38: 100nF; C_0603_1608Metric; MPN CC0603KRX7R9BB104; LCSC Part C14663; not fitted
C39, C41, C42: 10uF; C_0603_1608Metric; MPN CC0603MRX5R7BB106; LCSC Part C109457
D3: 60V 1A; D_SMA; MPN B120-13-F; LCSC Part C134421
D4: 1N4007-A7; D_SOD-123; MPN 1N4007 A7; LCSC Part C2902912
D5, D19, D20, D21: BAT54S; SOT-23; MPN BAT54S,215; LCSC Part C47546
D7: 1SMB5919BT3G; D_SMB; MPN 1SMB5919BT3G; LCSC Part C7422622
F1: 1A 60V; Fuse_1206_3216Metric; MPN CFS12V6TR50; LCSC Part C163133
IC4: CONN_02X08; DRV8825; not fitted
J1: 3-6437285-0; 364372850; Mouser Part Number 571-3-6437285-0
J2: USB_C_Receptacle_USB2.0_16P; USB_C_Receptacle_GCT_USB4105-xx-A_16P_TopMnt_Horizontal; MPN TYPE-C-31-M-12; LCSC Part C165948
J4: HM-10; PinSocket_1x06_P2.54mm_Vertical; LCSC Part C40877
JP7, JP8: Jumper_2_Open; SolderJumper-2_P1.3mm_Open_RoundedPad1.0x1.5mm; not fitted
LED5, LED6: RED; LED_0805_2012Metric; MPN NCD0805R1; LCSC Part C84256
P1: Conn_01x04; PinHeader_1x04_P2.54mm_Vertical; LCSC Part C5116483
R8, R16, R41, R43, R66: 10K; R_0603_1608Metric; LCSC Part C25804
R15, R69, R73: 1K; R_0603_1608Metric; LCSC Part C21190
R17: 2K7; R_0603_1608Metric; MPN RK73B1JTTD272J; LCSC Part C13167
R18, R62: 470R; R_0603_1608Metric; LCSC Part C23179
R38, R39: 0R; R_0603_1608Metric; LCSC Part C21189
R40: 1M; R_0603_1608Metric; LCSC Part C22935
R67: 10K; R_0603_1608Metric; MPN RK73B1JTTD272J; not fitted
R68: 22R; R_0603_1608Metric; MPN RK73B1JTTD272J; LCSC Part C23345; not fitted
R70: 120R; R_0603_1608Metric; MPN RK73B1JTTD272J; LCSC Part C22787
R71, R72: 5.1K; R_0603_1608Metric; MPN RC0805JR-075K1L; LCSC Part C23186
SW1: SW_Push; SW_Push_1P1T_NO_6x6mm_H9.5mm; MPN 6.0*6.0*6.0; LCSC Part C5127964
U1: L7805CDT(UMW); TO-252-2; MPN L7805CDT(UMW) Copy; LCSC Part C7394043
U2: STM32F407VETx; LQFP-100_14x14mm_P0.5mm; LCSC Part C28730
U4: W25Q16JVSS; SOIC-8_5.23x5.23mm_P1.27mm; not fitted
U5: TJA1050; SO-8_5.3x6.2mm_P1.27mm; LCSC Part C6952
U6: AMS1117-3.3; SOT-223-3_TabPin2; LCSC Part C6186
Y1: 8Mhz; Crystal_SMD_HC49-SD; MPN X49SM8MSD2SC; LCSC Part C12674
Y2: 32.768Khz; Crystal_SMD_3215-2Pin_3.2x1.5mm; MPN Q13FC13500004; LCSC Part C32346

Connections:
+3.3V: C12.2, C13.2, C15.2, C16.2, C21.2, C22.2, C23.2, C38.1, C42.1, C43.1, D5.2 (K), D19.2 (K), D20.2 (K), D21.2 (K), JP7.2 (B), JP8.2 (B), P1.1, R16.1, R38.2, R41.1, R67.1, U2.11 (VDD), U2.19 (VDD), U2.28 (VDD), U2.50 (VDD), U2.75 (VDD), U2.100 (VDD), U4.3 (IO2), U4.7 (IO3), U4.8 (VCC), U6.2 (VO); also elsewhere on the board
+5V: C5.1, C40.1, C41.1, C44.1, D4.1 (K), D7.1 (K), IC4.5, IC4.6, J1.10, J4.2, R18.1, U1.3 (OUT), U5.3 (vcc), U6.3 (VI); also elsewhere on the board
+12V: C4.1, D3.2 (A), F1.1, IC4.16, R17.2; also elsewhere on the board
+BATT: F1.2, J1.1; also elsewhere on the board
/BOOST: J1.33; also elsewhere on the board
/BOOT0: JP7.1 (A), R8.2, U2.94 (BOOT0)
/BOOT1: JP8.1 (A), R66.1, U2.37 (PB2)
/CLT: J1.28; also elsewhere on the board
/DIAHG: U2.81 (PD0); also elsewhere on the board
/DIR: IC4.8, U2.65 (PC8)
/ENBL: IC4.1, U2.63 (PC6)
/FUELP: J1.34; also elsewhere on the board
/F_CS: R67.2, U2.35 (PB0), U4.1 (~CS)
/HEAT_OUT-: U2.84 (PD3); also elsewhere on the board
/IAT: J1.29; also elsewhere on the board
/IDLE: J1.17; also elsewhere on the board
/IGN1: J1.4; also elsewhere on the board
/IGN2: J1.5; also elsewhere on the board
/INJ1: J1.30; also elsewhere on the board
/INJ2: J1.31; also elsewhere on the board
/LAUNCH: J1.19, R15.2
/O2: J1.26; also elsewhere on the board
/PA0: U2.23 (PA0); also elsewhere on the board
/PA1: U2.29 (PA4); also elsewhere on the board
/PA2: U2.30 (PA5); also elsewhere on the board
/PA3: U2.31 (PA6); also elsewhere on the board
/PA4: U2.32 (PA7); also elsewhere on the board
/PA5: U2.33 (PC4); also elsewhere on the board
/PA9: J4.5, U2.68 (PA9)
/PA10: D19.3 (COM), R62.1, U2.69 (PA10)
/PB8: R73.1, U2.95 (PB8)
/PB9: R69.1, U2.96 (PB9)
/PD4: U2.54 (PB15); also elsewhere on the board
/PD5: U2.53 (PB14); also elsewhere on the board
/PD6: U2.56 (PD9); also elsewhere on the board
/PD7: U2.55 (PD8); also elsewhere on the board
/PD8: U2.39 (PE8); also elsewhere on the board
/PD9: U2.40 (PE9); also elsewhere on the board
/PD10: U2.57 (PD10); also elsewhere on the board
/PD11: U2.58 (PD11); also elsewhere on the board
/PD12: U2.51 (PB12); also elsewhere on the board
/PD13: U2.52 (PB13); also elsewhere on the board
/PD14: U2.34 (PC5); also elsewhere on the board
/PD15: U2.62 (PD15)
/SCL: U2.47 (PB10)
/SDA: U2.48 (PB11)
/SPI1_MISO: U2.90 (PB4), U4.2 (DO(IO1))
/SPI1_MOSI: U2.91 (PB5), U4.5 (DI(IO0))
/SPI1_SCK: R68.1, U2.89 (PB3)
/SPI3_MISO: U2.79 (PC11); also elsewhere on the board
/SPI3_MOSI: U2.80 (PC12); also elsewhere on the board
/SPI3_SCK: U2.78 (PC10); also elsewhere on the board
/SS3: U2.7 (PC13); also elsewhere on the board
/STEP: IC4.7, U2.64 (PC7)
/STP-A1: IC4.12, J1.6
/STP-A2: IC4.11, J1.7
/STP-B1: IC4.13, J1.9
/STP-B2: IC4.14, J1.8
/SWCLK: P1.3, R43.1, U2.76 (PA14)
/SWDIO: P1.2, R41.2, U2.72 (PA13)
/TACHO: J1.14; also elsewhere on the board
/TPS: J1.27; also elsewhere on the board
/UA: U2.82 (PD1); also elsewhere on the board
/UR: U2.83 (PD2); also elsewhere on the board
/USB_D+: J2.A6 (D+), J2.B6 (D+), U2.71 (PA12)
/USB_D-: J2.A7 (D-), J2.B7 (D-), U2.70 (PA11)
/VR1-: J1.3; also elsewhere on the board
/VR2-: J1.12; also elsewhere on the board
/VVT: J1.32; also elsewhere on the board
CANH: J1.24, R70.2, U5.7 (CANH)
CANL: J1.25, R70.1, U5.6 (CANL)
Earth: IC4.15
GND: C4.2, C5.2, C12.1, C13.1, C15.1, C16.1, C21.1, C22.1, C23.1, C24.1, C25.1, C26.1, C27.1, C28.1, C29.1, C30.1, C31.1, C38.2, C39.2, C40.2, C41.2, C42.2, C43.2, C44.2, D5.1 (A), D7.2 (A), D19.1 (A), D20.1 (A), D21.1 (A), IC4.9, J1.11, J1.18, J1.20, J1.MH1, J1.MH2, J2.A1 (GND), J2.A12 (GND), J2.B1 (GND), J2.B12 (GND), J2.S1 (SHIELD), J4.3, LED5.1 (K), LED6.1 (K), P1.4, R8.1, R43.2, R66.2, R71.2, R72.2, SW1.1, U1.2 (GND), U2.10 (VSS), U2.20 (VSSA), U2.27 (VSS), U2.74 (VSS), U2.99 (VSS), U4.4 (GND), U5.2 (gnd), U5.8 (S), U6.1 (GND); also elsewhere on the board
HEAT-: J1.23; also elsewhere on the board
IA: J1.16; also elsewhere on the board
IP: J1.15; also elsewhere on the board
unnamed: D3.1 (K), U1.1 (IN)
unnamed: D5.3 (COM), R15.1, U2.59 (PD12)
unnamed: D20.3 (COM), R69.2, U5.1 (txd)
unnamed: D21.3 (COM), R73.2, U5.4 (rxd)
unnamed: J2.A8 (SBU1), R72.1
unnamed: J2.B8 (SBU2), R71.1
unnamed: J4.4, R62.2
unnamed: LED5.2 (A), R17.1
unnamed: LED6.2 (A), R18.2
unnamed: R68.2, U4.6 (CLK)
unnamed: R16.2, SW1.2, U2.14 (NRST)
unnamed: C31.2, U2.8 (PC14), Y2.2
unnamed: C30.2, U2.9 (PC15), Y2.1
unnamed: C26.2, R40.1, U2.12 (PH0), Y1.1
unnamed: C27.2, R40.2, U2.13 (PH1), Y1.2
unnamed: C28.2, U2.49 (VCAP_1)
unnamed: C29.2, U2.73 (VCAP_2)
unnamed: R39.2, U2.21 (VREF+)
UN: J1.21; also elsewhere on the board
VBUS: C39.1, D4.2 (A), J2.A4 (VBUS), J2.A9 (VBUS), J2.B4 (VBUS), J2.B9 (VBUS)
VDA: C24.2, C25.2, R38.1, R39.1, U2.22 (VDDA)
VM: J1.22; also elsewhere on the board
VR1+: J1.2; also elsewhere on the board
VR2+: J1.13; also elsewhere on the board

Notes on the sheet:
Bluetooth Header
Lambda LSU4.9
PROGRAMING
CAN
Main Connector
ZENER 5V
Stepper Module
Power Supply

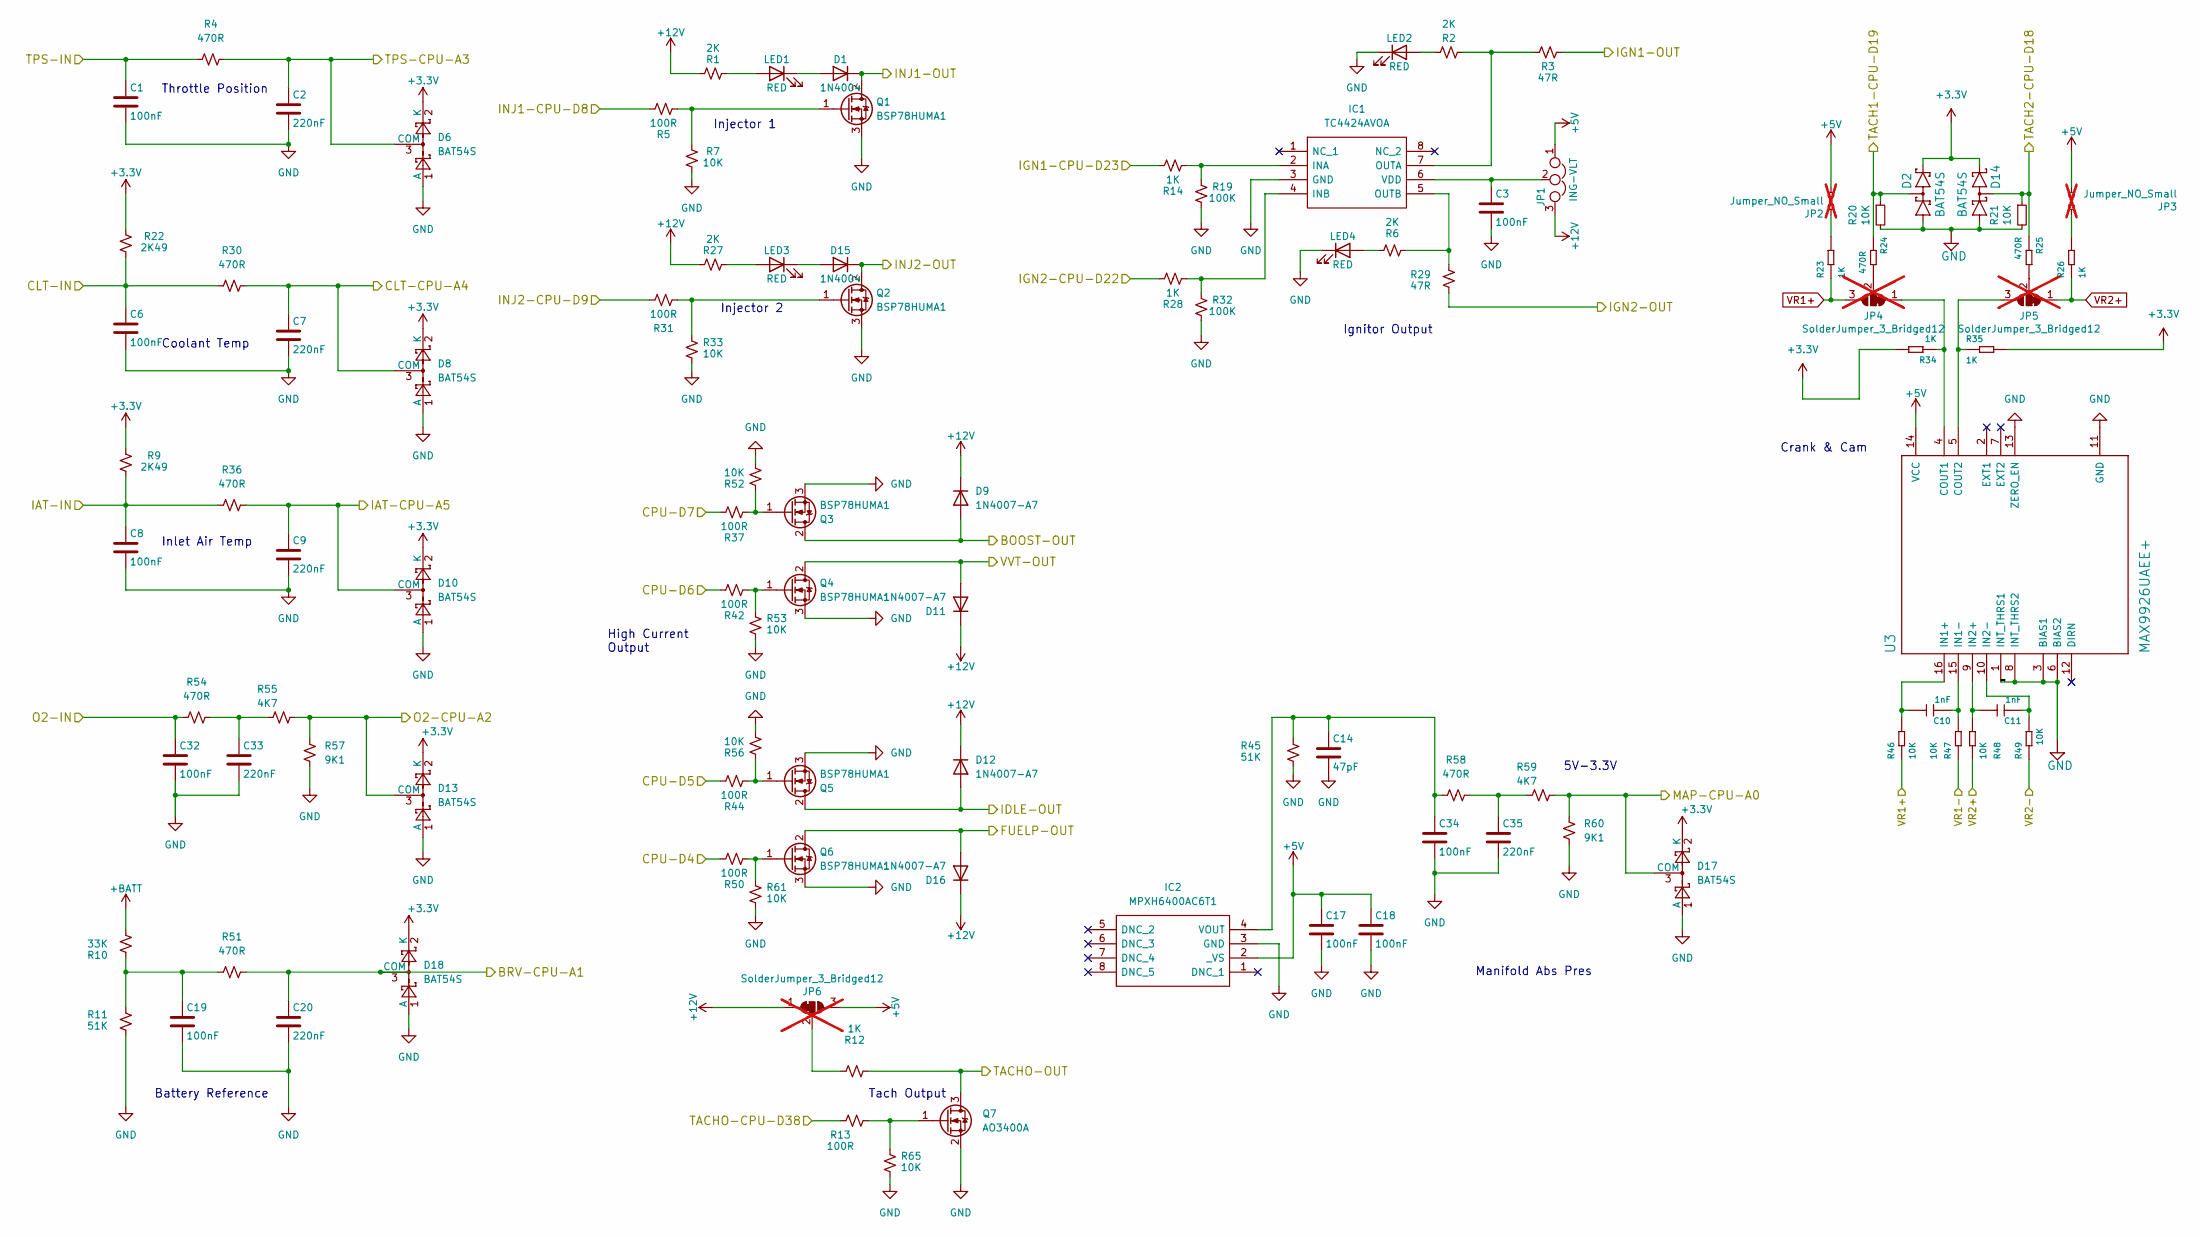
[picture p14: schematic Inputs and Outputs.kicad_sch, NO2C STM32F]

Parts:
C1, C3, C6, C8, C17, C18, C19, C32, C34: 100nF; C_0603_1608Metric; MPN CC0603KRX7R9BB104; LCSC Part C14663
C2, C7, C9, C20, C33, C35: 220nF; C_0603_1608Metric; MPN CC0603KRX7R9BB224; LCSC Part C107083
C10, C11: 1nF; C_0603_1608Metric; MPN 0603CG102J500NT; LCSC Part C1636
C14: 47pF; C_0603_1608Metric; MPN CC0603JRNPO9BN470; LCSC Part C105622
D1, D15: 1N4004; D_SMA; MPN 1N4004; LCSC Part C727080
D2, D6, D8, D10, D13, D14, D17, D18: BAT54S; SOT-23; MPN BAT54S,215; LCSC Part C47546
D9, D11, D12, D16: 1N4007-A7; D_SOD-123; MPN 1N4007 A7; LCSC Part C2902912
IC1: TC4424AVOA; SOIC127P600X175-8N; Mouser Part Number 579-TC4424AVOA
IC2: MPXH6400AC6T1; Mouser Part Number 841-MPXH6400AC6T1
JP1: ING-VLT; PinHeader_1x03_P2.54mm_Vertical; MPN 2.54-1*3P; LCSC Part C49257
JP2, JP3: Jumper_NO_Small; SolderJumper-2_P1.3mm_Open_Pad1.0x1.5mm; not fitted
JP4, JP5, JP6: SolderJumper_3_Bridged12; SolderJumper-3_P1.3mm_Bridged12_Pad1.0x1.5mm; not fitted
LED1, LED2, LED3, LED4: RED; LED_0805_2012Metric; MPN NCD0805R1; LCSC Part C84256
Q1, Q2, Q3, Q4, Q5, Q6: BSP78HUMA1; SOT-223-3_TabPin2; MPN BSP78HUMA1; LCSC Part C2653794
Q7: AO3400A; SOT-23; MPN AO3400A; LCSC Part C344010
R1, R2, R6, R27: 2K; R_0603_1608Metric; LCSC Part C22975
R3, R29: 47R; R_0603_1608Metric; LCSC Part C23182
R4, R24, R25, R30, R36, R51, R54, R58: 470R; R_0603_1608Metric; LCSC Part C23179
R5, R13, R31, R37, R42, R44, R50: 100R; R_0603_1608Metric; LCSC Part C22775
R7, R20, R21, R33, R46, R47, R48, R49, R52, R53, R56, R61, R65: 10K; R_0603_1608Metric; LCSC Part C25804
R9, R22: 2K49; R_0603_1608Metric; LCSC Part C22908
R10: 33K; R_0603_1608Metric; LCSC Part C4216
R11, R45: 51K; R_0603_1608Metric; LCSC Part C23196
R12, R14, R23, R26, R28, R34, R35: 1K; R_0603_1608Metric; LCSC Part C21190
R19, R32: 100K; R_0603_1608Metric; LCSC Part C25803
R55, R59: 4K7; R_0603_1608Metric; LCSC Part C23162
R57, R60: 9K1; R_0603_1608Metric; LCSC Part C23260
U3: MAX9926UAEE+; SOP64P602X175-16N; LCSC Part C1523548

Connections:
+3.3V: D2.2 (C2), D6.2 (K), D8.2 (K), D10.2 (K), D13.2 (K), D14.2 (C2), D17.2 (K), D18.2 (K), R9.1, R22.1, R34.2, R35.2; also elsewhere on the board
+5V: C17.1, C18.1, IC2.2 (_VS), JP1.1, JP2.2, JP3.2, JP6.3 (B), U3.14 (VCC); also elsewhere on the board
+12V: D9.1 (K), D11.1 (K), D12.1 (K), D16.1 (K), JP1.3, JP6.1 (A), R1.2, R27.2; also elsewhere on the board
+BATT: R10.1; also elsewhere on the board
/BOOST: D9.2 (A), Q3.2 (D); also elsewhere on the board
/CLT: C6.1, R22.2, R30.1; also elsewhere on the board
/FUELP: D16.2 (A), Q6.2 (D); also elsewhere on the board
/IAT: C8.1, R9.2, R36.1; also elsewhere on the board
/IDLE: D12.2 (A), Q5.2 (D); also elsewhere on the board
/IGN1: R3.2; also elsewhere on the board
/IGN2: R29.2; also elsewhere on the board
/INJ1: D1.1 (K), Q1.2 (D); also elsewhere on the board
/INJ2: D15.1 (K), Q2.2 (D); also elsewhere on the board
/O2: C32.1, R54.1; also elsewhere on the board
/PA0: D17.3 (COM), R59.2, R60.2; also elsewhere on the board
/PA1: C20.1, D18.3 (COM), R51.2; also elsewhere on the board
/PA2: D13.3 (COM), R55.2, R57.2; also elsewhere on the board
/PA3: C2.1, D6.3 (COM), R4.2; also elsewhere on the board
/PA4: C7.1, D8.3 (COM), R30.2; also elsewhere on the board
/PA5: C9.1, D10.3 (COM), R36.2; also elsewhere on the board
/PD4: R50.2; also elsewhere on the board
/PD5: R44.2; also elsewhere on the board
/PD6: R42.2; also elsewhere on the board
/PD7: R37.2; also elsewhere on the board
/PD8: R5.2; also elsewhere on the board
/PD9: R31.2; also elsewhere on the board
/PD10: D14.3 (C1A2), R21.1, R25.1; also elsewhere on the board
/PD11: D2.3 (C1A2), R20.1, R24.1; also elsewhere on the board
/PD12: R28.2; also elsewhere on the board
/PD13: R14.2; also elsewhere on the board
/PD14: R13.1; also elsewhere on the board
/TACHO: Q7.3 (D), R12.1; also elsewhere on the board
/TPS: C1.1, R4.1; also elsewhere on the board
/VR1-: R47.1; also elsewhere on the board
/VR2-: R49.1; also elsewhere on the board
/VVT: D11.2 (A), Q4.2 (D); also elsewhere on the board
GND: C1.2, C2.2, C3.2, C6.2, C7.2, C8.2, C9.2, C14.2, C17.2, C18.2, C19.2, C20.2, C32.2, C33.2, C34.2, C35.2, D2.1 (A1), D6.1 (A), D8.1 (A), D10.1 (A), D13.1 (A), D14.1 (A1), D17.1 (A), D18.1 (A), IC1.3 (GND), IC2.3 (GND), LED2.1 (K), LED4.1 (K), Q1.3 (S), Q2.3 (S), Q3.3 (S), Q4.3 (S), Q5.3 (S), Q6.3 (S), Q7.2 (S), R7.2, R11.2, R19.2, R20.2, R21.2, R32.2, R33.2, R45.2, R52.2, R53.2, R56.2, R57.1, R60.1, R61.2, R65.2, U3.1 (INT_THRS1), U3.3 (BIAS1), U3.6 (BIAS2), U3.8 (INT_THRS2), U3.11 (GND), U3.13 (ZERO_EN); also elsewhere on the board
unnamed: C19.1, R10.2, R11.1, R51.1
unnamed: C33.1, R54.2, R55.1
unnamed: C35.1, R58.2, R59.1
unnamed: D1.2 (A), LED1.1 (K)
unnamed: D15.2 (A), LED3.1 (K)
unnamed: IC1.2 (INA), R14.1, R19.1
unnamed: IC1.4 (INB), R28.1, R32.1
unnamed: IC1.7 (OUTA), R2.1, R3.1
unnamed: IC1.5 (OUTB), R6.1, R29.1
unnamed: C3.1, IC1.6 (VDD), JP1.2
unnamed: C14.1, C34.1, IC2.4 (VOUT), R45.1, R58.1
unnamed: JP2.1, R23.2
unnamed: JP3.1, R26.2
unnamed: JP4.1 (A), R34.1, U3.4 (COUT1)
unnamed: JP4.2 (C), R24.2
unnamed: JP5.3 (B), R35.1, U3.5 (COUT2)
unnamed: JP5.2 (C), R25.2
unnamed: JP6.2 (C), R12.2
unnamed: LED1.2 (A), R1.1
unnamed: LED2.2 (A), R2.2
unnamed: LED3.2 (A), R27.1
unnamed: LED4.2 (A), R6.2
unnamed: Q1.1 (G), R5.1, R7.1
unnamed: Q2.1 (G), R31.1, R33.1
unnamed: Q3.1 (G), R37.1, R52.1
unnamed: Q4.1 (G), R42.1, R53.1
unnamed: Q5.1 (G), R44.1, R56.1
unnamed: Q6.1 (G), R50.1, R61.1
unnamed: Q7.1 (G), R13.2, R65.1
unnamed: C10.2, R46.2, U3.16 (IN1+)
unnamed: C10.1, R47.2, U3.15 (IN1-)
unnamed: C11.2, R48.2, U3.9 (IN2+)
unnamed: C11.1, R49.2, U3.10 (IN2-)
VR1+: JP4.3 (B), R23.1, R46.1; also elsewhere on the board
VR2+: JP5.1 (A), R26.1, R48.1; also elsewhere on the board

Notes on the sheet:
Manifold Abs Pres
Throttle Position
High Current Output
Tach Output
5V-3.3V
Injector 2
Battery Reference
Coolant Temp
Ignitor Output
Crank & Cam
Injector 1
Inlet Air Temp

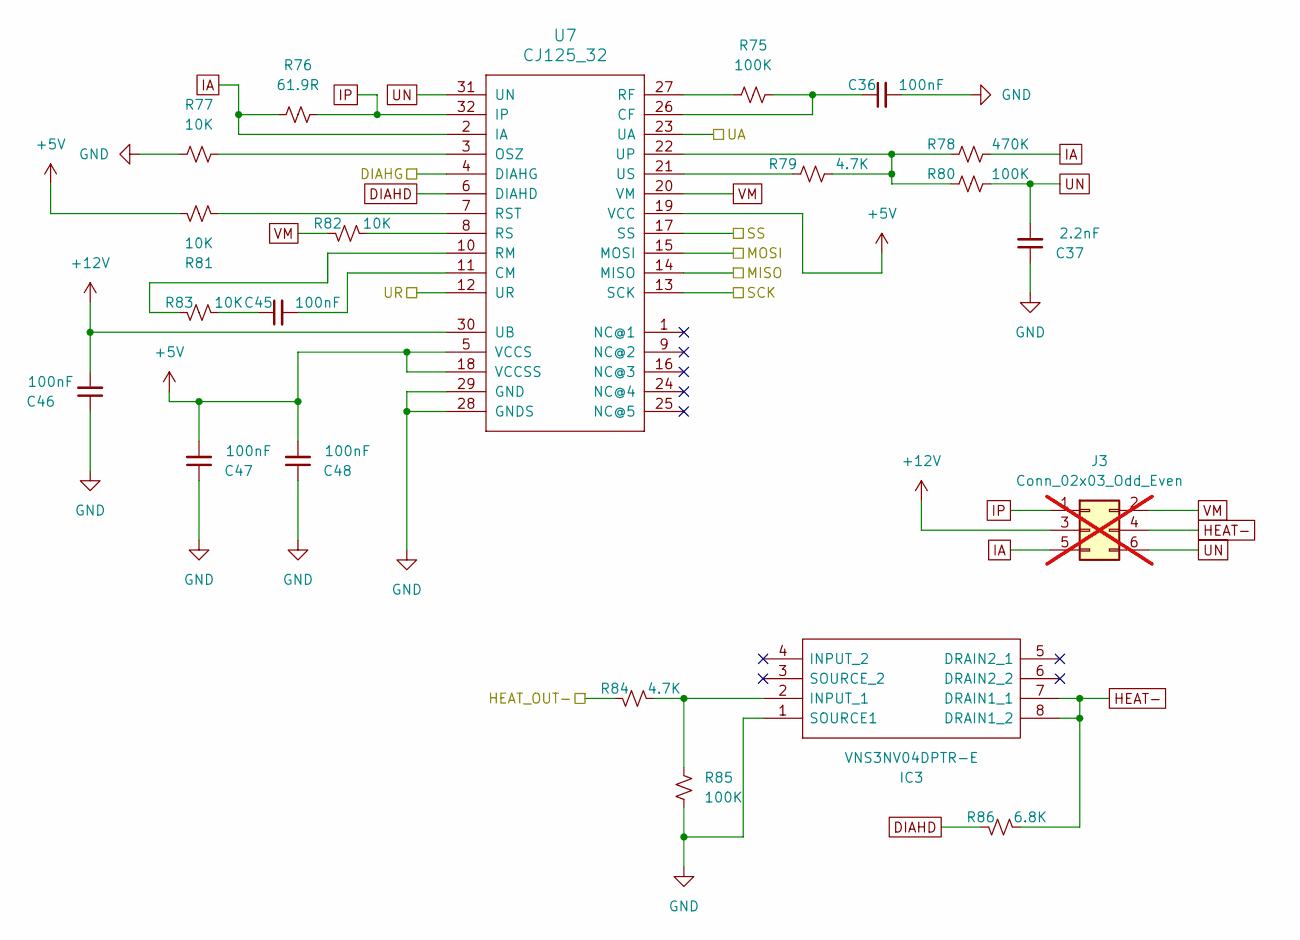
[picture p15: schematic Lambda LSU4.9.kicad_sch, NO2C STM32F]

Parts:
C36, C45, C46, C47, C48: 100nF; C_0603_1608Metric; MPN CC0603KRX7R9BB104; LCSC Part C14663
C37: 2.2nF; C_0603_1608Metric; LCSC Part C309517
IC3: VNS3NV04DPTR-E; SOIC127P600X175-8N; Mouser Part Number 511-VNS3NV04DPTR-E
J3: Conn_02x03_Odd_Even; PinHeader_2x03_P2.54mm_Vertical; not fitted
R75, R80, R85: 100K; R_0603_1608Metric; LCSC Part C25803
R76: 61.9R; R_0603_1608Metric; LCSC Part C23092
R77, R81, R82, R83: 10K; R_0603_1608Metric; LCSC Part C25804
R78: 470K; R_0603_1608Metric; LCSC Part C365173
R79, R84: 4.7K; R_0603_1608Metric; LCSC Part C99782
R86: 6.8K; R_0603_1608Metric; LCSC Part C26004
U7: CJ125_32; LQFP-32_5x5mm_P0.5mm; LCSC Part C18198890

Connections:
+5V: C47.2, C48.2, R81.1, U7.5 (VCCS), U7.18 (VCCSS), U7.19 (VCC); also elsewhere on the board
+12V: C46.2, J3.3, U7.30 (UB); also elsewhere on the board
/DIAHG: U7.4 (DIAHG); also elsewhere on the board
/HEAT_OUT-: R84.1; also elsewhere on the board
/SPI3_MISO: U7.14 (MISO); also elsewhere on the board
/SPI3_MOSI: U7.15 (MOSI); also elsewhere on the board
/SPI3_SCK: U7.13 (SCK); also elsewhere on the board
/SS3: U7.17 (SS); also elsewhere on the board
/UA: U7.23 (UA); also elsewhere on the board
/UR: U7.12 (UR); also elsewhere on the board
DIAHD: R86.1, U7.6 (DIAHD)
GND: C36.2, C37.1, C46.1, C47.1, C48.1, IC3.1 (SOURCE1), R77.1, R85.1, U7.28 (GNDS), U7.29 (GND); also elsewhere on the board
HEAT-: IC3.7 (DRAIN1_1), IC3.8 (DRAIN1_2), J3.4, R86.2; also elsewhere on the board
IA: J3.5, R76.1, R78.2, U7.2 (IA); also elsewhere on the board
IP: J3.1, R76.2, U7.32 (IP); also elsewhere on the board
unnamed: C45.1, R83.2
unnamed: IC3.2 (INPUT_1), R84.2, R85.2
unnamed: C36.1, R75.2, U7.26 (CF)
unnamed: C45.2, U7.11 (CM)
unnamed: R77.2, U7.3 (OSZ)
unnamed: R75.1, U7.27 (RF)
unnamed: R83.1, U7.10 (RM)
unnamed: R82.2, U7.8 (RS)
unnamed: R81.2, U7.7 (RST)
unnamed: R78.1, R79.2, R80.1, U7.22 (UP)
unnamed: R79.1, U7.21 (US)
UN: C37.2, J3.6, R80.2, U7.31 (UN); also elsewhere on the board
VM: J3.2, R82.1, U7.20 (VM); also elsewhere on the board

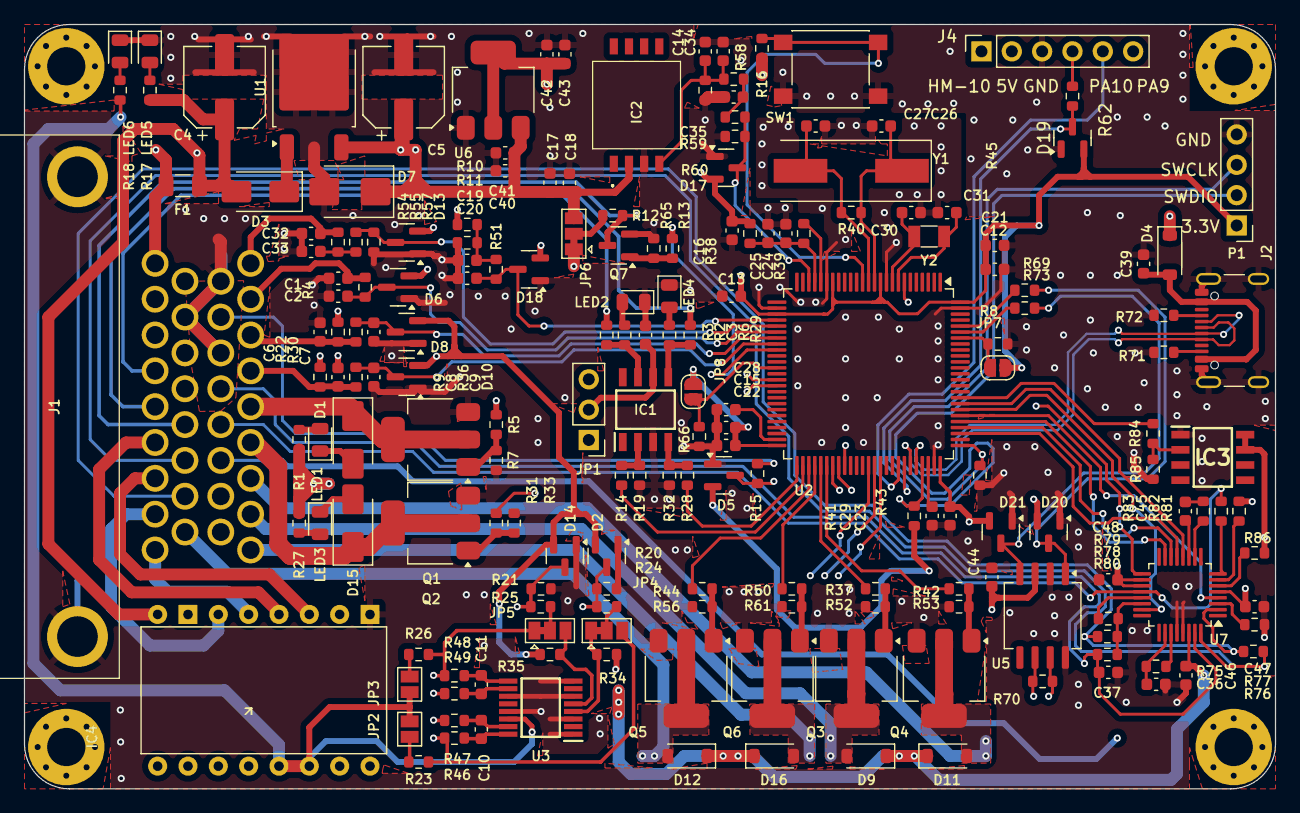
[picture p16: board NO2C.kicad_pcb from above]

Board: 4 copper layers, 104.8 x 64.0 mm, 188 parts (0 on the bottom side), 136 nets.

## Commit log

2024-10-30 Draft DD
    [BOM-NO2C.csv, INS.kicad_sch, INS.sch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]
2024-10-30 quick parts supply update
    [BOM-NO2C.csv, Inputs and Outputs.kicad_sch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]
2024-10-30 read me update
    [BOM-NO2C.csv, MPX4250AP.step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]
2024-10-31 step file update
    [BOM-NO2C.csv, Inputs and Outputs.kicad_sch, NO2C-2018-08-18-14-43-34.sch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]
2024-10-31 clean up
    Removed older and duplicate files. Added Step File in a zip
    [BOM-NO2C.csv, Inputs and Outputs.kicad_sch, NO2C-2018-08-18-14-43-34.sch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]
2024-11-18 Updated with WB
    LSU 4.9 wideband integration
    [BOM-NO2C.csv, Inputs and Outputs.kicad_sch, Lambda LSU4.9.kicad_sch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]
2024-11-18 Wideband file clean up
    Organized file structure and general updates and cleaned.
    [BOM-NO2C.csv, Inputs and Outputs.kicad_sch, Lambda LSU4.9.kicad_sch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]
2024-11-23 plugin wideband
    Added wide band to the main connector.
    [BOM-NO2C.csv, Lambda LSU4.9.kicad_sch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]
2024-11-23 Wideband integrated
    Cleaned up file structure and included wide band upload
    [BOM-NO2C.csv, Inputs and Outputs.kicad_sch, Lambda LSU4.9.kicad_sch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]
2025-01-12 Bluetooth added
    [BOM-NO2C.csv, Inputs and Outputs.kicad_sch, Lambda LSU4.9.kicad_sch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]
2025-01-12 Bluetooth
    Added
    [BOM-NO2C.csv, Inputs and Outputs.kicad_sch, Lambda LSU4.9.kicad_sch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]
